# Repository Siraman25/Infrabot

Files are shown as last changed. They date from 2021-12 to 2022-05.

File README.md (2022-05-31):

# **Infrarot-Roboter**
## **Beschreibung**
Bei diesen Inrarot-Robotern handelt es sich um zwei auf Rädern fahrenden Robotern welche als "Shooter-Spiel" konzipiert sind. Sie werden über zwei ESP-32 gesteuert (ESP32-CAM & ESP32-S2). Bedient werden sie entweder mit einem PS3-Controller oder über eine Website via PC oder Smartphone. Die Steuerung über PS3-Controller wird durch eine Bluetooth-Verbindung zwischen Controller und ESP32-S2 realisiert.\
Sie können sich gegenseitig abschießen. Dies wird mit Infrarot-Empfänger und -Sender realisiert. Für ein akustisches Feedback für Fehler, Schuss und Treffer werden Buzzer verwendet.\
Die Räder werden mit zwei 360°-Servomotoren angetriebn. Diese besitzen drei Pins: GND, +5V, Steuersingal. Die beiden Pins GND und +5V werden direkt an den Spannungsregler angeschlossen, da ein Servomotor ca. 550mA Strom zieht. Der Pin für das Steuersignal wird an den ESP32-S2 angeschlossen.\
Über eine Webseite, die auf dem ESP-S2 läuft, kann man den Videostream des ESP-CAM sehen.

Der Ordner "ESP32-CAM Code" enthält das funktionierende Code, im "Debug Code" Ordner befinden sich unwichtige Programme und Sketches, die wir fürs Debugging und fürs Testen benutzt haben. Der Ordner "ESP32-S2 Code" enthält das getestete Code für den ESP32-S2, dieser sollte einwandfrei funktionieren. Leider konnten wir es nicht aufbauen. Im "Web-Interface"-Ordner befindet sich der Boilerplate für die Web-Interface und eine kleine Dokumentation, wie das ausschauen hätte sollen. Dazu gibt es noch den Doku-Ordner.

## **Beschreibung**
##### Servo
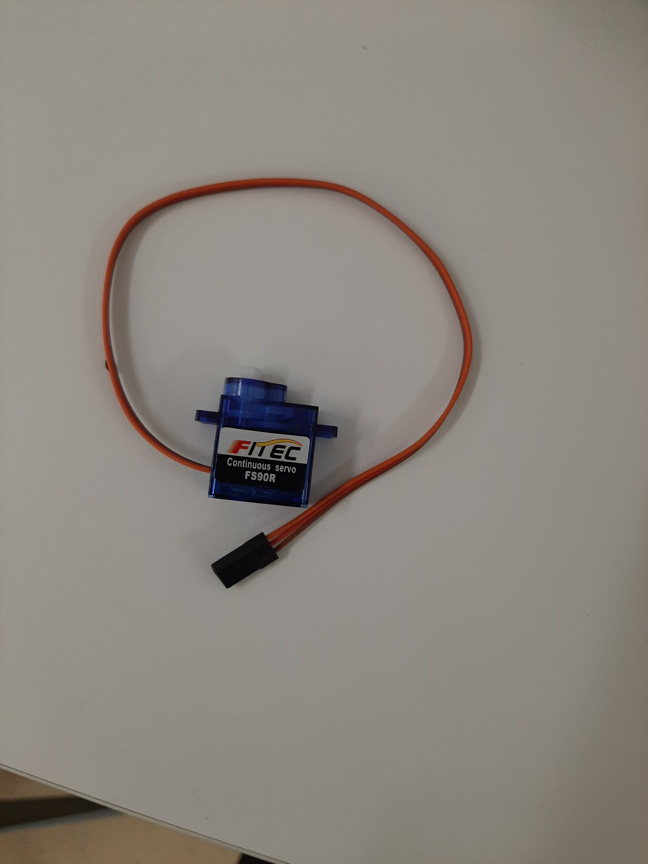
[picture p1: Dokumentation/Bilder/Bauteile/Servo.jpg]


<code>Name</code>: Continous servo FS90R
<code>Preis</code>: € 21,81	(4 Stück)
<code>Link</code>: [Click-here](https://it.aliexpress.com/item/32984667875.html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)
##### Batteriehalterung
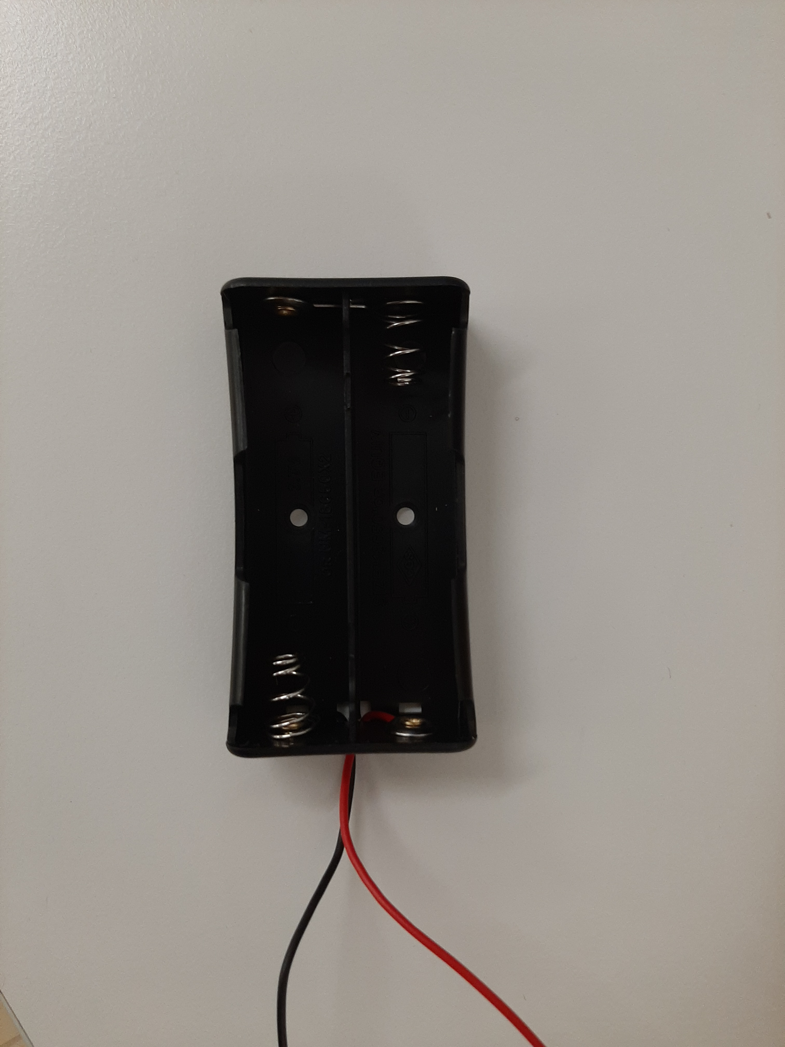
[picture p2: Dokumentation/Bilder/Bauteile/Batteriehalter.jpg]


<code>Name</code>: 
<code>Preis</code>: 
<code>Link</code>: [Click-here]()
##### Powermanagement

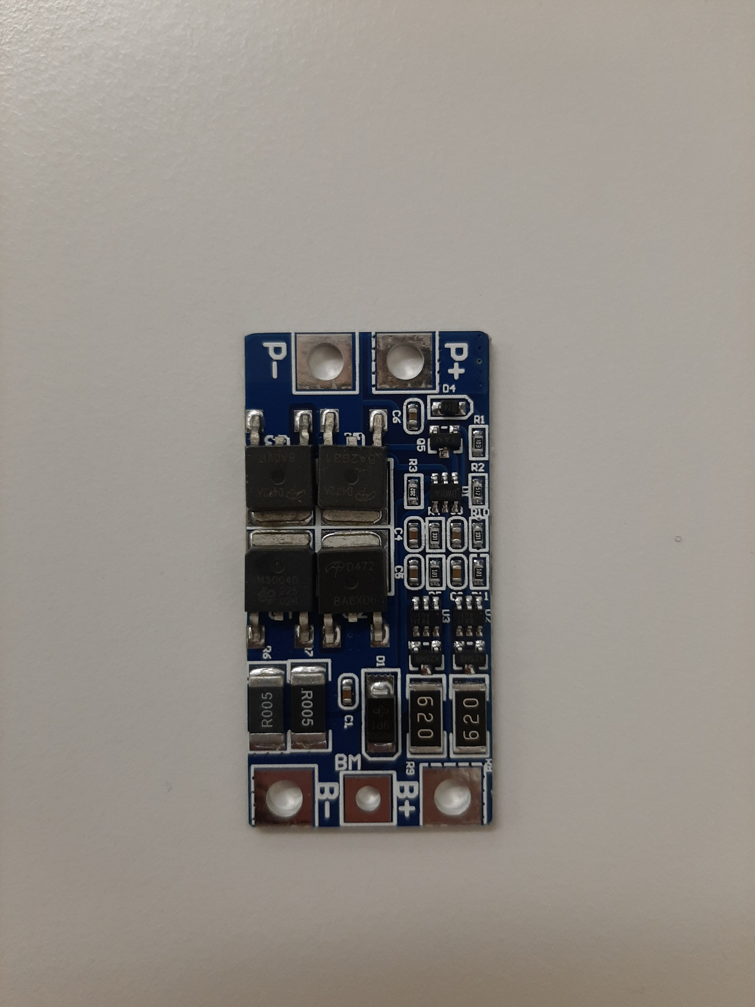
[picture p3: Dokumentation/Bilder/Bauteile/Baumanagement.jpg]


<code>Name</code>: 
<code>Preis</code>: 
<code>Link</code>: [Click-here]()
##### ESP32 Cam-Module
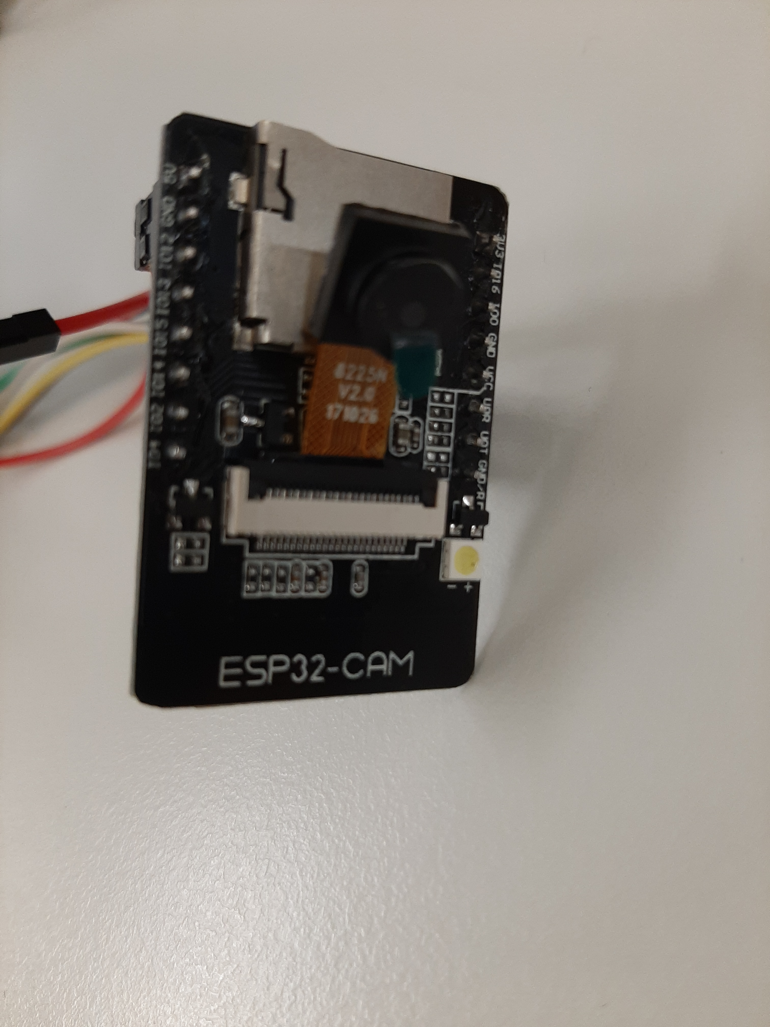
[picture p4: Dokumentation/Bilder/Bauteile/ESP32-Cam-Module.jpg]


<code>Name</code>: 113990580
<code>Preis</code>: € 8,99000 (1 Stück)
<code>Link</code>: [Click-here](https://www.digikey.it/it/products/detail/seeed-technology-co-ltd/113990580/9697033)
##### Hilfsrad
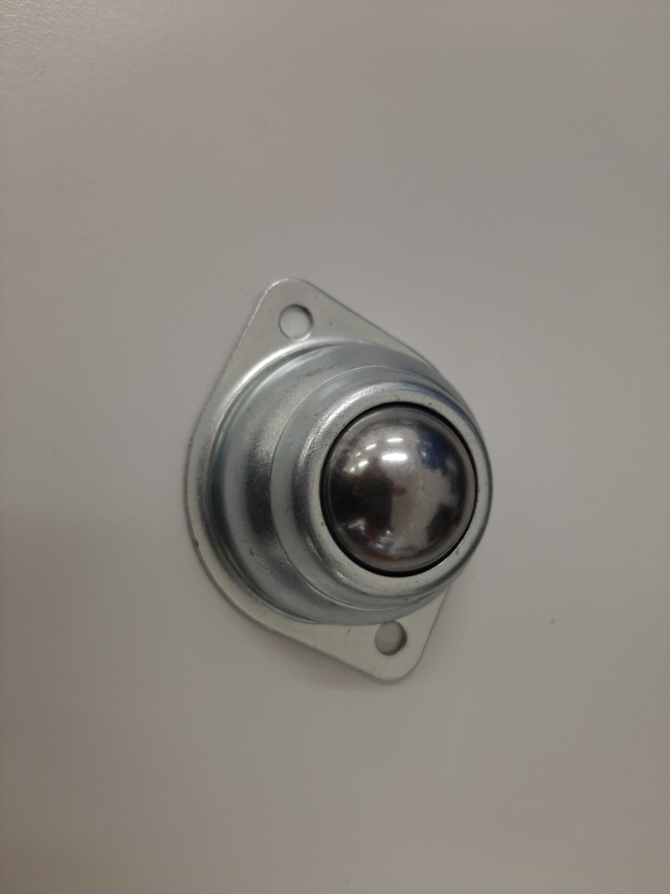
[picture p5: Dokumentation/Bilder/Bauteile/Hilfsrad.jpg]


<code>Name</code>:  Universalrad
<code>Preis</code>:  € 5,95
<code>Link</code>: [Click-here](https://it.aliexpress.com/item/4001072165757.html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,scm-url:1007.13338.183347.0,pvid:666dd3e0-f355-4ce7-bd33-32656806e43c,tpp_buckets:668%232846%238111%231996&&pdp_ext_f=%7B%22sceneId%22:%2223416%22,%22sku_id%22:%2210000014060064385%22%7D)
##### Infrarot LED
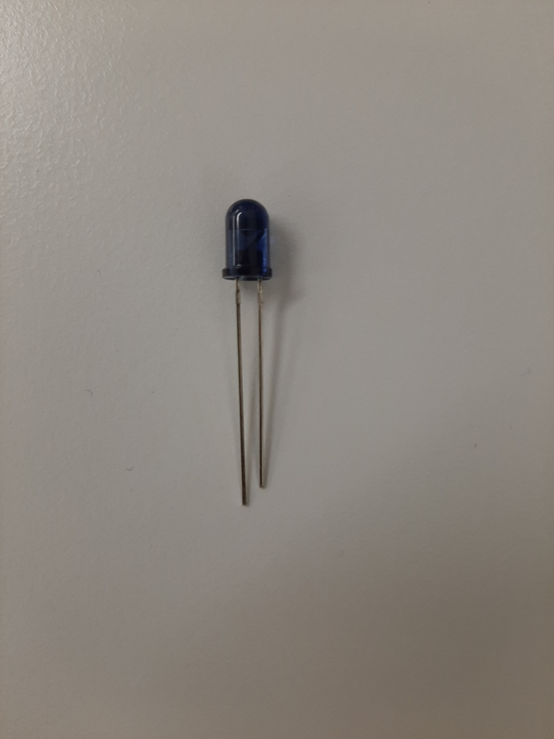
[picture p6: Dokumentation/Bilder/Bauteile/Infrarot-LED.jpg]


<code>Name</code>: # TSAL6100
<code>Preis</code>: € 0,47000 (1 Stück)
<code>Link</code>: [Click-here](https://www.digikey.it/it/products/detail/vishay-semiconductor-opto-division/TSAL6100/1681338)
##### Infrarot Reciever
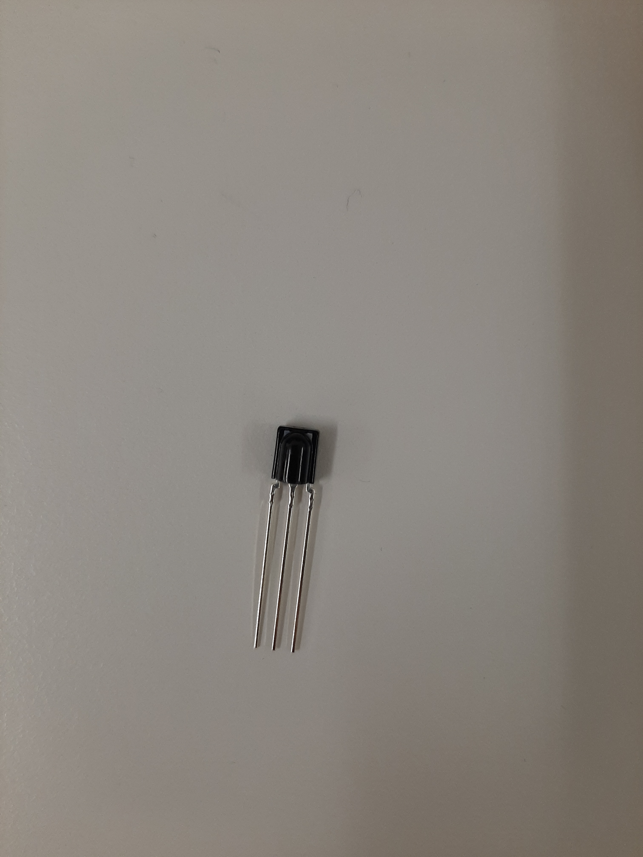
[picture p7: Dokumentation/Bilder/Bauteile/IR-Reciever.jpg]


<code>Name</code>: TSSP58038
<code>Preis</code>: € 1,42000 (1 Stück)
<code>Link</code>: [Click-here](https://www.digikey.it/it/products/detail/vishay-semiconductor-opto-division/TSSP58038/4695717)
##### Button
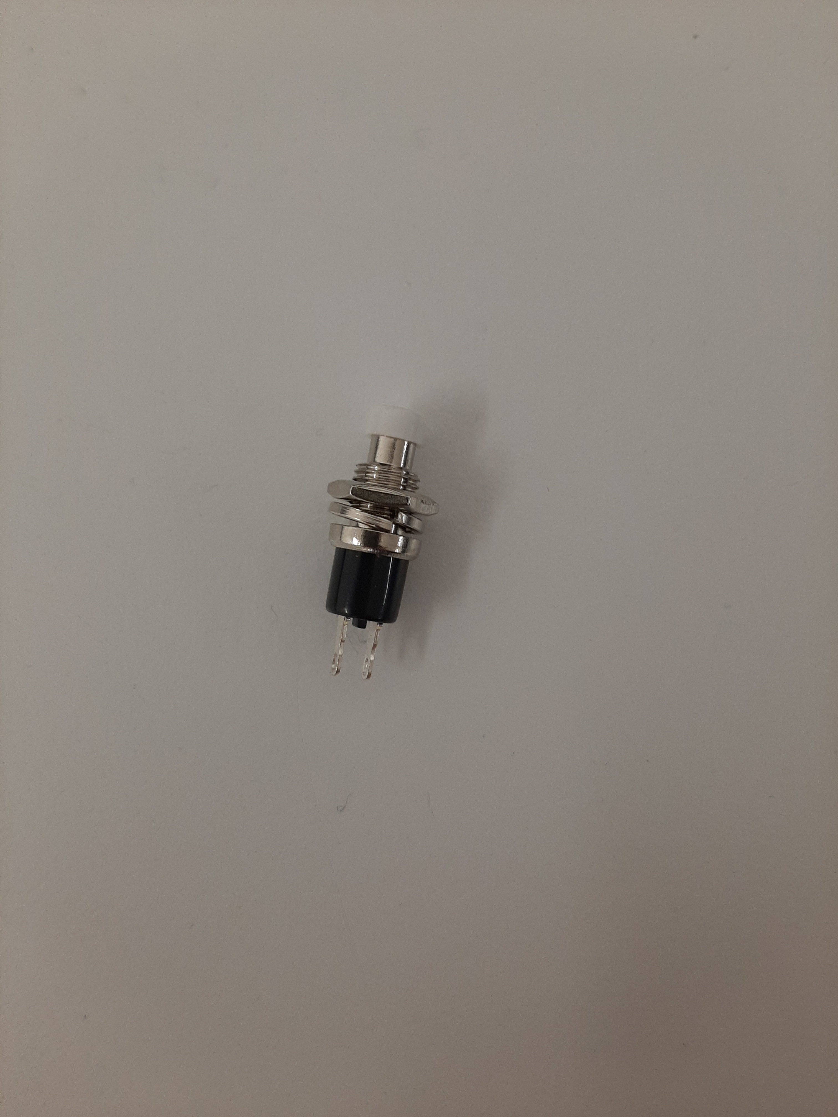
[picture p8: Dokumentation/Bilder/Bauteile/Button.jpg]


<code>Name</code>: 
<code>Preis</code>: 
<code>Link</code>: [Click-here]()
##### Switch
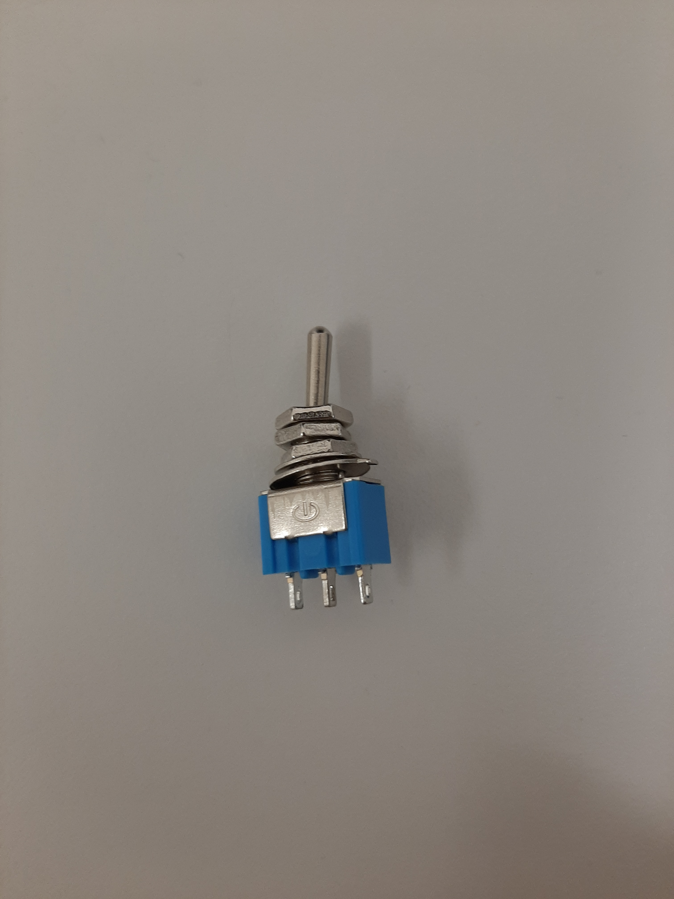
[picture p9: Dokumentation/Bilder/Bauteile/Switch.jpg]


<code>Name</code>: 
<code>Preis</code>: 
<code>Link</code>: [Click-here]()
##### Kühler
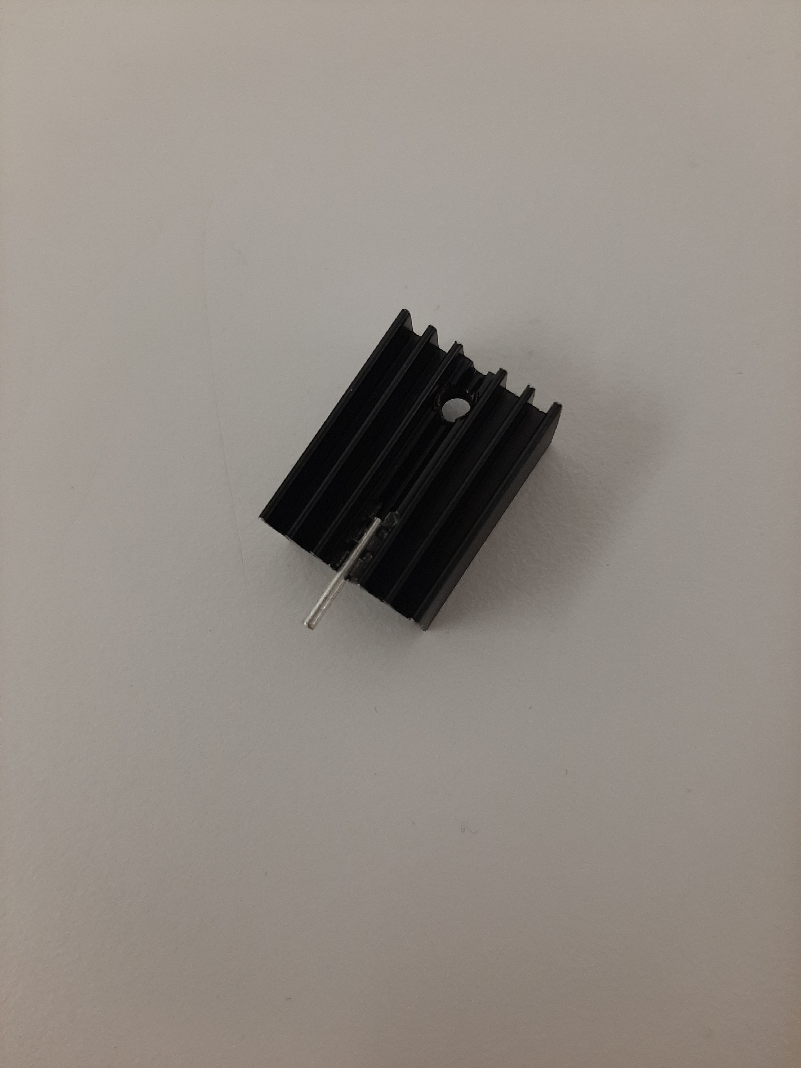
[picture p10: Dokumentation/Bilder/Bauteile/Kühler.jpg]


<code>Name</code>:  PS3-Controller
<code>Preis</code>: 
<code>Link</code>: [Click-here]()
##### Spannungsregler
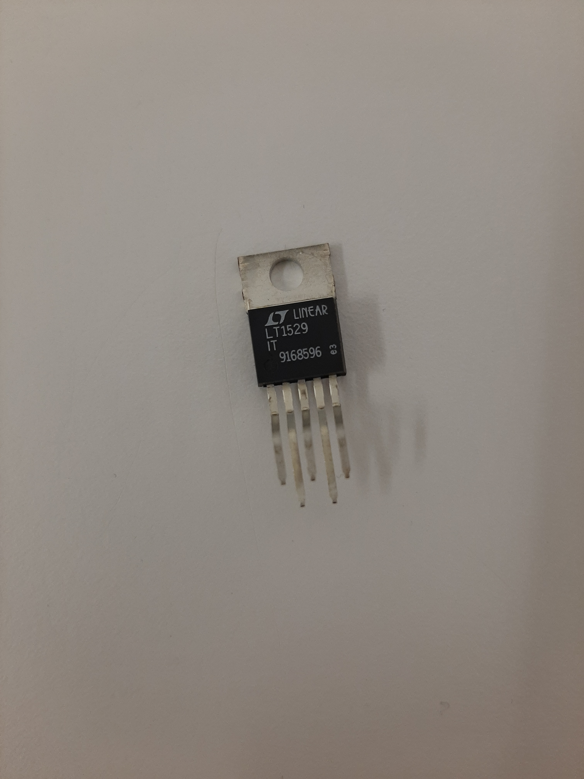
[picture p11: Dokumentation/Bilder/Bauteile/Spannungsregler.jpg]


<code>Name</code>:  LT1529-5
<code>Preis</code>: 
<code>Link</code>: [Click-here]()

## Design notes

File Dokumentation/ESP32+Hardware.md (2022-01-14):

#PS3-Controller
##Funktionen
Der Linke Joystick ist für die steuerung des Robos zuständig

#360° Servo (FS90R)
##Verkabelung
Servo1: Pin D12
Servo2: Pin D14

#Librarys
####Servo.h
#### GitHub: https://github.com/RoboticsBrno/ServoESP32
####PS3_Controller_Host-1.1.0

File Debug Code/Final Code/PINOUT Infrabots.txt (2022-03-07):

PINOUT Infrabots:

ESP32-S2
GND -> GND_PLATINE
5V -> 5V_PLATINE
3.3V -> 3.3V_PLATINE
38 -> RESET_PIN_IN
39 -> IR_REC
40 -> IR_SEND
41 -> HWSerial_0       (RX S2, TX CAM)
42 -> HWSerial_1       (TX S2, RX CAM)

ESP32-CAM
GND -> GND_PLATINE
U0T -> SERIAL_TX_UPLOAD
U0R -> SERIAL_RX_UPLOAD
IO0 -> PIN0_UPLOAD
3.3V -> 3.3V_PLATINE
IO2 -> SERVO1
IO14 -> HWSerial_0      (TX S2, RX CAM)
IO13 -> HWSerial_1      (RX S2, TX CAM)
IO12 -> SERVO2
5V -> 5V_PLATINE

Alle GNDs der einzelnen Boards müssen sicherheitshalber auf der Platine verbunden werden.

Weitere Verbindungen:
IR_SEND:
IR_SEND -> BC337 (Transistor) Base // 3.3V_PLATINE -> BC337 Collector // BC337 Emitter -> IR-LED -> 20 OHM-Widerstand (2*10 Ohm) -> GND_PLATINE

IR_REC:
IR-Receiver+ -> 5V_PLATINE // IR-Receiver- -> GND_PLATINE // IR-Receiver_DATA -> IR_REC

SERVOS:
SERVO+ -> 5V_PLATINE // SERVO- -> GND_PLATINE // SERVO_DATA -> SERVOxx

RESET_PIN_IN:
GND_PLATINE -> 10kOhm -> RESET_PIN_IN (Pull-down-Widerstand) // Switch-button+ -> 5V_PLATINE // Switch-button- -> RESET_PIN_IN

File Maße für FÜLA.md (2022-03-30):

- Platine:
	- Länge= 127mm
	- Breite= 65mm
	- Höhe= 2mm
- Hinterrad:
	- Durchmesser<sub>GROẞ</sub>= 70mm
	-  Durchmesser<sub>KLEIN</sub>= 52mm
	-  Höhe= 30mm
	-  Durchmesser Kugel= 40mm
-  Servo:
	-  Länge= 23mm
	-  Breite= 22mm
	-  Höhe= 12mm
		-  Ecken:
			-  Länge= 3mm
			-  Breite= 5mm
			-  Höhe= 12mm
			-  Versatz Vorderkante= 4mm
-  Vorderrad:
	-  Durchmesser= 60mm
	-  Breite= 7mm
-  Batteriebehälter
	-  Länge= 75mm
	-  Breit= 40mm
	-  Höhe= 18mm

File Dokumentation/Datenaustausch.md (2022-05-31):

# Datenaustausch
Der PS3-Controller wird über Bluetooth mit ESP32-CAM verbunden. Der ESP32-CAM steuert die beiden Servos. Der ESP-S2 ist über Hardware-Serial mit dem ESP32-CAM verbunden. Für das Empfangen und Senden des Infrarotsignals ist der ESP32-S2 zuständig.\
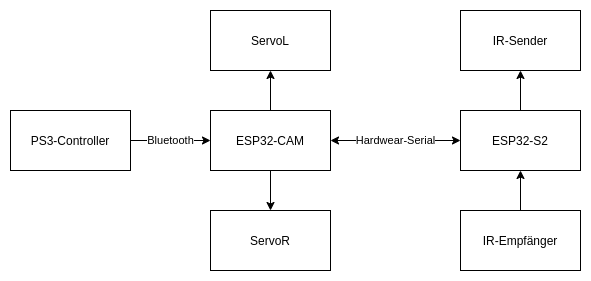
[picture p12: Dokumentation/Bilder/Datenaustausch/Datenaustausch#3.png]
Datenaustausch
 

Da wir den ESP32-S2 nicht implementiert haben funktioniert der Infrarot nicht und die ganze rechte Seite dieses Bildes wird nicht benötigt.

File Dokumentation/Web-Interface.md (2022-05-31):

# Web-Interface
Die Web-Interface zeigt das Video-Feed des ESP32-CAM-Moduls, im Code vom ESP32-CAM werden die verschiedenen Video-Einstellungen eingestellt.
Die originelle Idee wäre die gewesen, dass man den Punktestand der zwei Roboter sieht. Diese Funktion wurde allerdings nicht implementiert, da es ohne Infrarot-System (bzw. ohne 2. Roboter) keinen Sinn ergibt, die Punkte zu zählen.
Als basis der HTML-Datei wurde die standard-Library des ESP32-CAM benutzt. Dann wurde der Container des Video-Feeds geändert, um die Möglichkeit, vom Browser Einstellungen zu ändern, zu entfernen.

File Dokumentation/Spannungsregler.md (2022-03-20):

# Spannungsregler

Verwendeter Spannungsregler: LT1529

## Charakterisitics
* V<sub>Out</sub>= 3,3V - 14V
* I<sub>Max</sub>= 3A
* V<sub>DropOut<sub>Min</sub></sub> at I<sub>Max</sub>= >0,6V
* Thermisches Limit= 125°

## Verwendung und Package
Package: CT

 Spannungsregler_Package
 
 Verwendung:
 
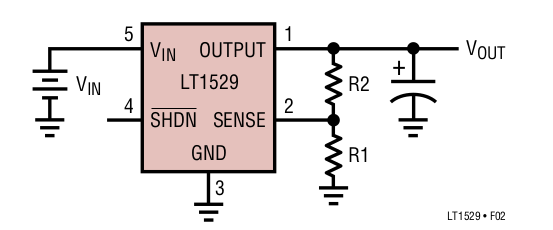
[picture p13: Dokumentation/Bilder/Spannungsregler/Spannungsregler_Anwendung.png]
Spannungsregler_Anwendung
 
 
 ## Pins
 * **OUTPUT**: 
 Dieser Pin Liefert die Spannung (V<sub>Out</sub>) und den Strom für die Last. Der 22$\mu$F Elektrolykondensator wird verwendet um Schwingungen zu vermeiden.
 * **SENSE**:
 Dieser Pin ist auch als ADJ-Pin bekannt. Zur Wahl der Ausgangsspannung wird hier ein Spannungsteiler eingebaut.
 * **GND**:
 Über den GND-Pin fällt die Spannung V<sub>DO</sub> ab. V<sub>DO</sub> ist die Differenz zwischen V<sub>In</sub> und V<sub>Out.
 * **<span style="text-decoration:overline">SHDN</span>**: 
 Der <span style="text-decoration:overline">SHDN</span> Pin ist für das Ein- bzw. Ausschalten des Gerätes zuständig. Bekommt diser Pin ein High-Signal so ist der Spannungsregler aktiv. Bei einem Low-Signal ist er inaktiv.
 * **V<sub>IN</sub>**:
 V<sub>IN</sub> ist der Input-Pin. Über ihn fließt die zu regulierende Eingangspannung (V<sub>In</sub>).

## Berechnung des Spannungsteilers
**Gegeben:**
U<sub>OUT</sub>= 5V\
U<sub>R1</sub>= 3,75V\
U<sub>R2</sub>= 1,25V\
I<sub>SENSE</sub>= 150nA
	
**Wahl:**
R<sub>1</sub>= 100kΩ
	
**Rechnung:**
	I<sub>R1</sub> = U<sub>R1</sub> : R<sub>1</sub> -> 3,75V : 100kΩ = 37,5µA\
	I<sub>R2</sub> = I<sub>R1</sub> - I<sub>SENSE</sub> -> 37,5µA - 150nA = 37,35µA\
	R<sub>2</sub> = U<sub>R2</sub> : I<sub>R2</sub> -> 1,25V : 37,35µA = 33467,202Ω ≈ 33kΩ
	
**Probe:**
	U<sub>OUT</sub> = U<sub>R1</sub> x (1 + (R<sub>2</sub> : R<sub>1</sub>)) + (I<sub>SENSE</sub> x R<sub>2</sub>) -> 3,75V x (1 + (33kΩ : 100kΩ)) +(150nA x 33kΩ) = 4,99245V
	
## Thermische Probleme

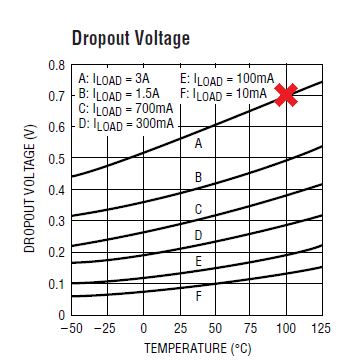
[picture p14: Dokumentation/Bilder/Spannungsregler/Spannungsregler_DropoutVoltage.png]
Spannungsregler_DropoutVoltage

	
Bei einem maximalen Ausgangsstrom von 3A und einer Abfallsspannung von 0,7V erreicht der Spannungsregler eine Temperatur von 100°. Da wir unseren aber mit einer höheren Abfallsspannung zurechtkommen muss, werden wir ohne Kühlung das thermische Limit von 125° überschreiten. Um eine thermische Zerstörung zu vermeiden verwende wir einen Kühler für das Package TO-220. 

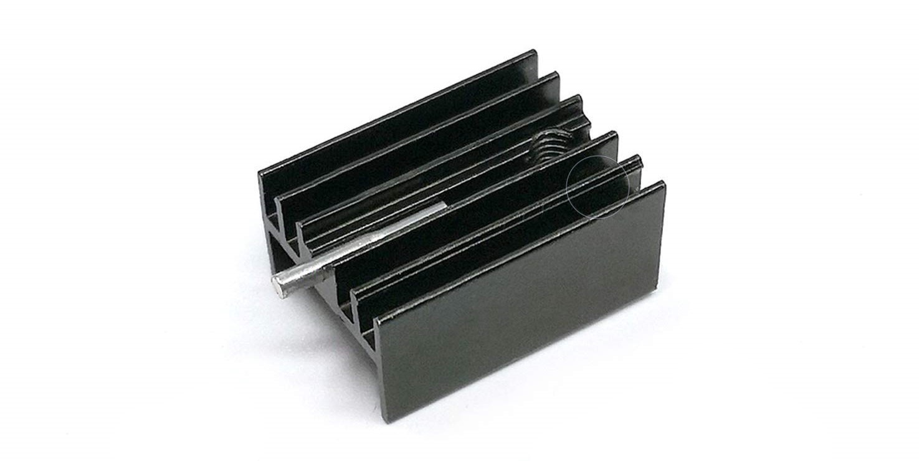
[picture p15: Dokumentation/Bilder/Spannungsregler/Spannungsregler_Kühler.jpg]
Spannungsregler_Kühler


Dies ist ein Low-Profile Aluminium Kühlkörper, der P<sub>Kühler</sub> = 3W Leistung and die Umgebung abgibt.
	
## **Leistungsberechnung**
	
Thermischer Widerstand:
Spannungsregler_ThermischerWiderstand
	
**Gegeben:**
	V<sub>In</sub> = 6,7V\
	V<sub>OUT</sub> = 5V
	I<sub>GES</sub> = 2,5A\
	P<sub>Kühler</sub> = 3W\
	T<sub>Umgebung</sub>≈ 30°C\
	
**Rechnung:**
	U<sub>DropOut</sub> = V<sub>In</sub> - V<sub>Out</sub> -> 6,7V - 5V = 1,7V\
	P<sub>GES</sub> = U<sub>DropOut</sub> x I<sub>GES</sub> -> 1,7V x 2,5A = 4,25W\
	P<sub>VR</sub> = P<sub>GES</sub> - P<sub>Kühler</sub> -> 4,25W - 3W = 1,25W\
	T<sub>VR</sub> = P<sub>VR</sub> x 50°C/W -> 1,25W x 50°C/W = 62,5°C\
	T<sub>GES</sub> = T<sub>Umgebung</sub> + T<sub>VR</sub> -> 30°C + 62,5°C = 92,5°C

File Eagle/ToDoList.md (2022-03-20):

- [ ]   extra Pins
- [ ]   extra Leds (statusleds)
- [ ]   virtual serial
- [ ]   Vorwiedertsände berechnen
- [ ]   pins für buzzers
- [ ]   Löcher an den Ecken zur Fixierung der Platine

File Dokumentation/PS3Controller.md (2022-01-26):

# Steuerung der Motoren mit einem Ps3 Controller

## **Biblioteken**

> **Ps3_Controller.h** (https://github.com/jvpernis/esp32-ps3)

* <code>Ps3.begin("MAC_Adresse");</code> ist dazu da die mac adresse des Ps3controllers dem esp32 zu geben, damit dieser sich mit dem Controller verbinden kann.
* <code>Ps3.attachOnConnect(onConnect);</code> ist dazu da in einem void **(onConnect)** zu springen aus dem erst wieder herrausgesprungen wird sobalt der Controller verbunden ist.
* <code>Ps3.attach(notify);</code> ist dazu da in den void **(notify)** zu springen wo die Knöfe und Joysticks des Controllers ausgelesen werden.
* <code>Ps3.event.analog_change.button.l1</code> ist dazu da den shoulderbutton in einem analogwert auszulesen. das **l1** am ende kann mit **r1**, **r2**, **l2** ausgewechselt werden je nachdem welcher button ausgelesen werden soll.
* <code>Ps3.data.analog.stick.rx</code>: dieser Befehl ließt die Werte des Joysticks aus. **rx** kann mit **ry**, **ly**, **lx** ausgewechselt werden je nachdem welcher Joystick und welche achsen des Joysticks benötigt werden. Die X-Achse gibt werte von **-128(links)** bis **127(rechts)** aus.Die Y-Achse gibt auchh die Werte **-128(vorne)** bis **127(hinten)** aus.
* <code>Ps3.data.button.cross</code>: dieser Befehl liest den **X** button auf der rechten Seite des Controllers aus. Wenn mann **"cross"** mit **"triangle"**, **"square"** oder **"circle"** austauscht werden die andern 3 buttons ausgelesen.

>  **Servo.h** (https://www.arduino.cc/reference/en/libraries/servo/) 
* <code>servo[].write("0,90 oder 180");</code> Diese Funktion ist dafür da den Servo die Informationen zu geben in welche richtung er sich drehen soll. In den Klammern wird **90** geschrieben fals der Servo stehen bleiben soll, **180** wenn er sich mit höchster geschwindigkeit in eine Richtung bewegen soll und **0** wenn er mit höchster geschwindigkeit in die andere Richtung fahren soll. 
* <code>static const int servosPins[2]; = {"PinSero1, PinServo2"};</code> In dieser Funktion werden die Pins an denen die Servos angeschlossen werden declariert. 
* <code>Servo servos[2];</code> In den eckigen Klammern wir die anzahl wie viele Servos verwendet werden angegeben.

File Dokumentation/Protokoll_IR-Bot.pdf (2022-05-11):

Aris Mandolini | Juri Ladurner | Max Dandler

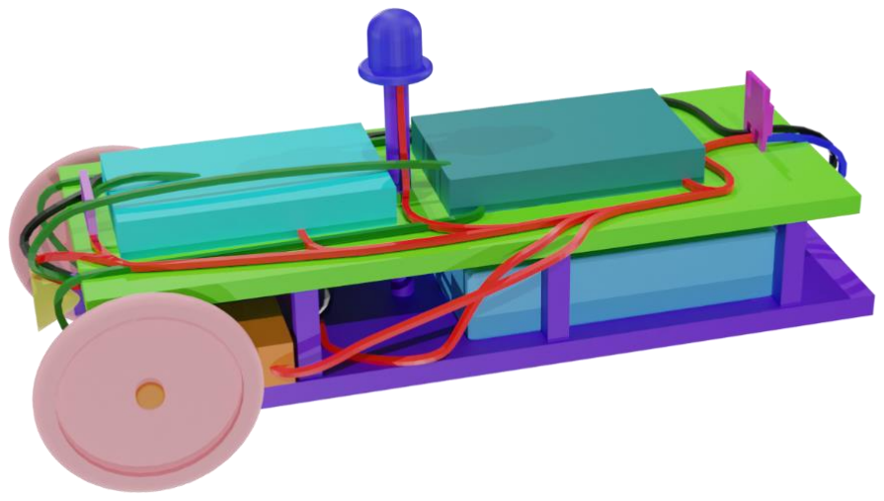
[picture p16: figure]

FÜLA: IR-Bot | 2021/22

## IR-Bot

Protokoll

Anlagenschema:

Beschreibung:

Dieses Projekt besteht aus zwei identischen Fahrzeugen. Es sind zwei fahrbare Roboter, welche auf drei Rädern stehen. Die beiden vorderen Rädern sind an 360°-Servos gekoppelt, welche für die Bewegung des Roboters verantwortlich sind. Das hintere Rad ist nur zur Stabilisierung da. Gesteuert wird der Roboter mithilfe eines PS3-Controllers. Dieser verbindet sich via Bluetooth an den ESP32-Cam. Der ESP32-Cam steuert auch die beiden Servo-Motoren. Der ESP32-Cam ist mit Hardware-Serial mit dem ESP32-S2 verbunden und erhält über diese Datenlinie Daten vom ESP32-S2. Der ESP32-S2 steuert den Infrarot-Receiver und den Infrarot-Transmitter. Der Infrarot-Transmitter ist das “Gewehr” des Roboters. Der Receiver empfängt die ausgesandten Lichtwellen.

HMI:

schießen

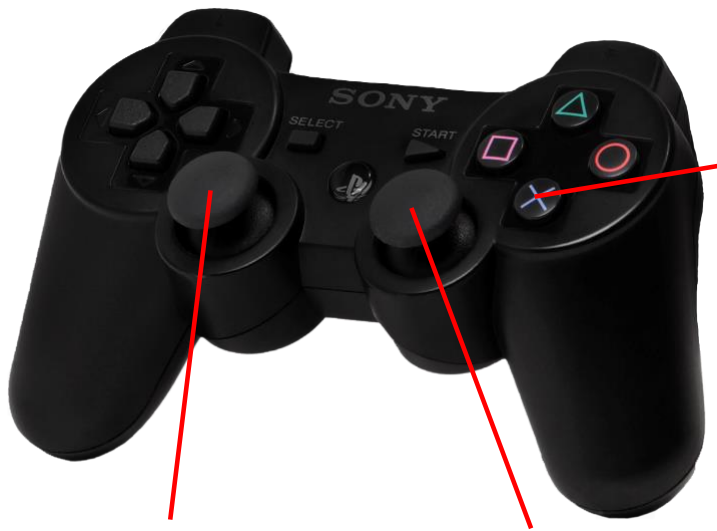
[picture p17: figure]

Servo-Links | Servo-Rechts

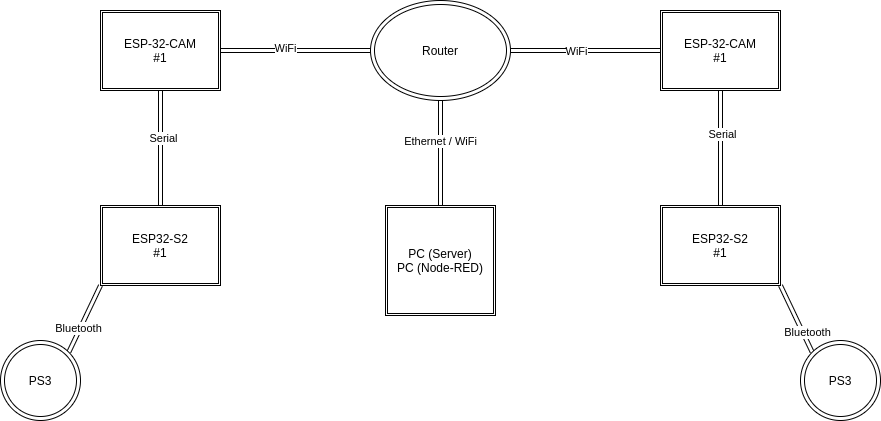
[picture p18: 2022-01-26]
Web-Interface/Network.drawio.png

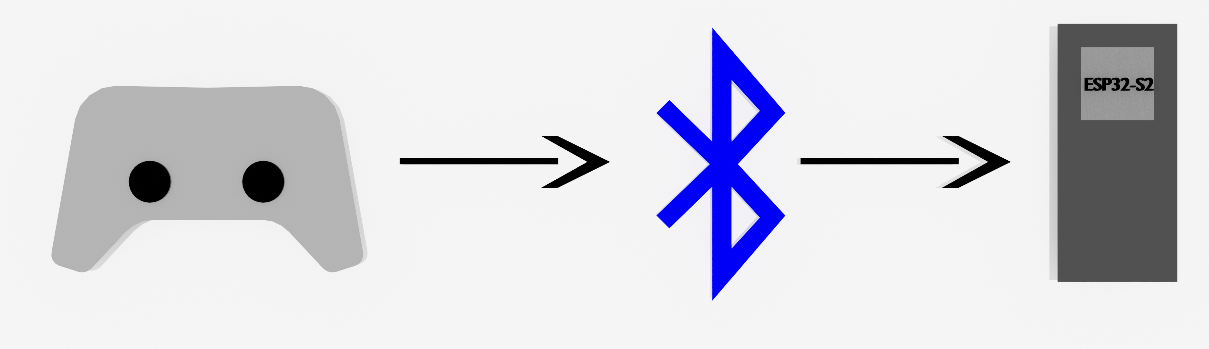
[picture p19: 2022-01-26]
Dokumentation/Bilder/Readme/Connection_PS3_ESP32.png

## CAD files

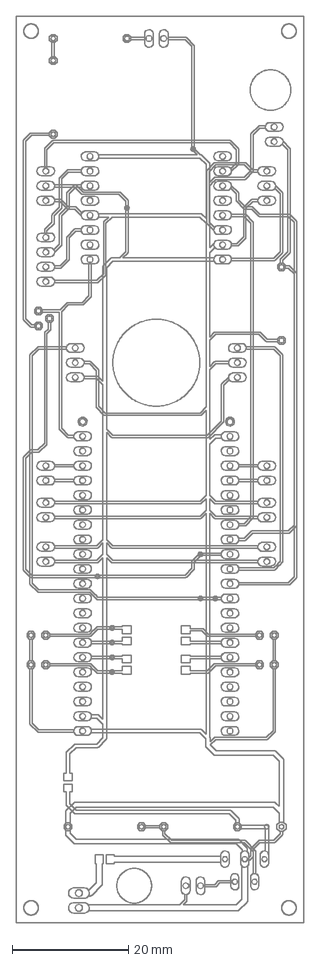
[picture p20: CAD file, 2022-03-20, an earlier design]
Eagle/V3/Spannungsversorgung_V3_#3.dxf
49.5 x 156.2 mm

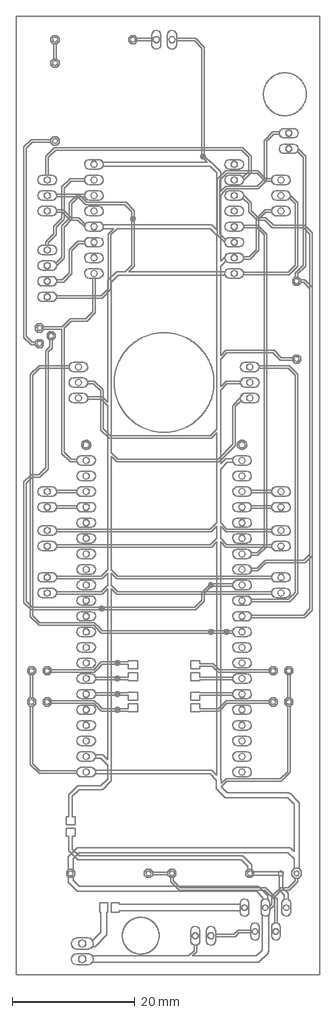
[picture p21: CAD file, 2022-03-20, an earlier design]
Eagle/V3/Spannungsversorgung_V3_#2.dxf
49.5 x 156.2 mm

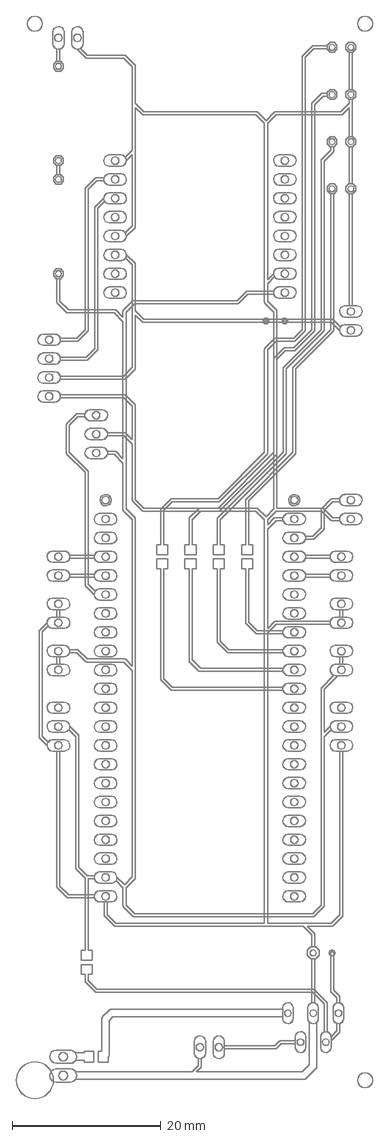
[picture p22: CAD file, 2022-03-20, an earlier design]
Eagle/V3/Spannungsversorgung_V3_#1.dxf
48.0 x 145.7 mm

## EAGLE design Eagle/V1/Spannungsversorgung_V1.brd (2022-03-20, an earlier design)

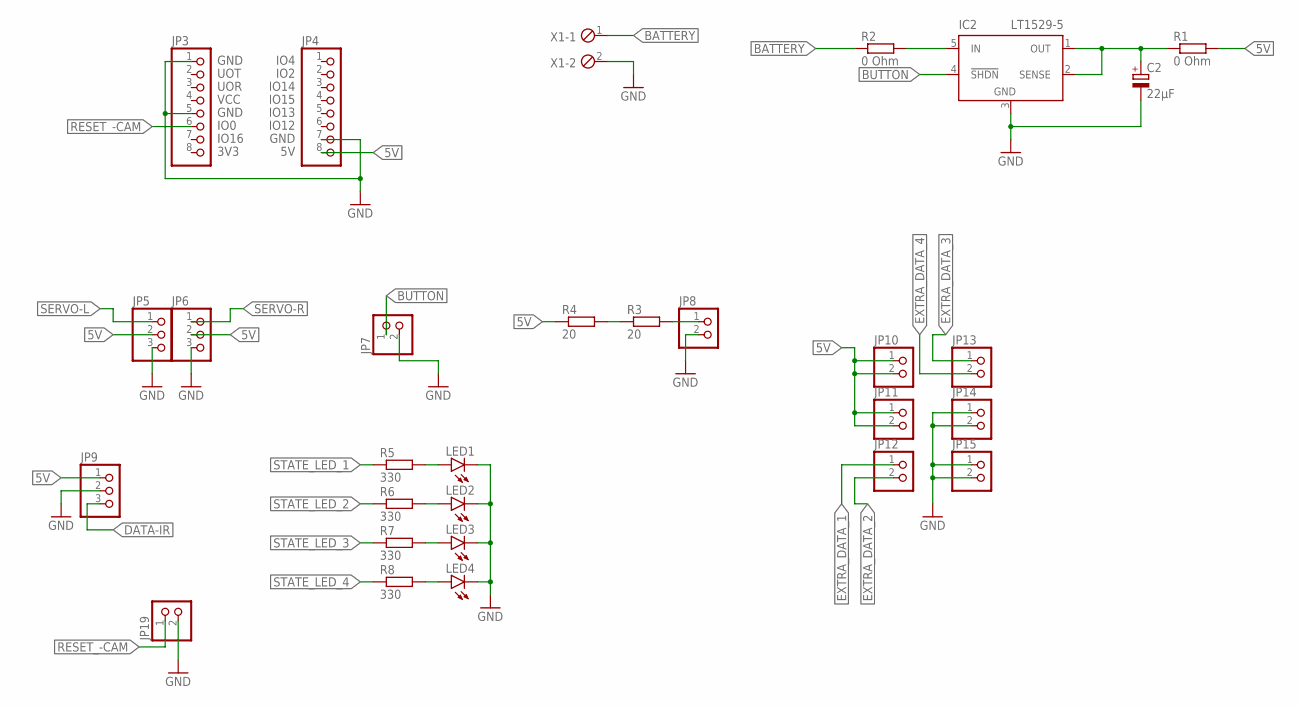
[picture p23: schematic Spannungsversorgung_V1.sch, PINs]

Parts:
C2: 22µF; E2,5-5
IC2: LT1529-5; TO220-5
JP3, JP4: PINHD-1X8; 1X08
JP5, JP6, JP9: PINHD-1X3; 1X03
JP7, JP8, JP10, JP11, JP12, JP13, JP14, JP15, JP19: PINHD-1X2; 1X02
LED1, LED2, LED3, LED4: LED3MM
R1, R2: 0 Ohm; R0805
R3, R4: 20; 0309/12
R5, R6, R7, R8: 330; R0805
X1: MPT2; 2POL254

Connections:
5V: JP4.8, JP5.2, JP6.2, JP9.1, JP10.1, JP10.2, JP11.1, JP11.2, R1.2, R4.1
BATTERY: R2.1, X1.1
BUTTON: IC2.4 (!SHDN), JP7.1
DATA-IR: JP9.3
EXTRA_DATA_1: JP12.1
EXTRA_DATA_2: JP12.2
EXTRA_DATA_3: JP13.1
EXTRA_DATA_4: JP13.2
GND: C2.-, IC2.3 (GND), JP3.1, JP3.5, JP4.7, JP5.3, JP6.3, JP7.2, JP8.2, JP9.2, JP14.1, JP14.2, JP15.1, JP15.2, JP19.2, LED1.K (C), LED2.K (C), LED3.K (C), LED4.K (C), X1.2
unnamed: R3.1, R4.2
unnamed: JP8.1, R3.2
unnamed: IC2.5 (IN), R2.2
unnamed: C2.+, IC2.1 (OUT), IC2.2 (SENSE), R1.1
unnamed: LED1.A, R5.2
unnamed: LED2.A, R6.2
unnamed: LED3.A, R7.2
unnamed: LED4.A, R8.2
RESET_-CAM: JP3.6, JP19.1
SERVO-L: JP5.1
SERVO-R: JP6.1
STATE_LED_1: R5.1
STATE_LED_2: R6.1
STATE_LED_3: R7.1
STATE_LED_4: R8.1

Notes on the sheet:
3V3
IO16
IO0
GND
VCC
UOR
UOT
IO12
IO13
IO15
IO14
IO2
IO4

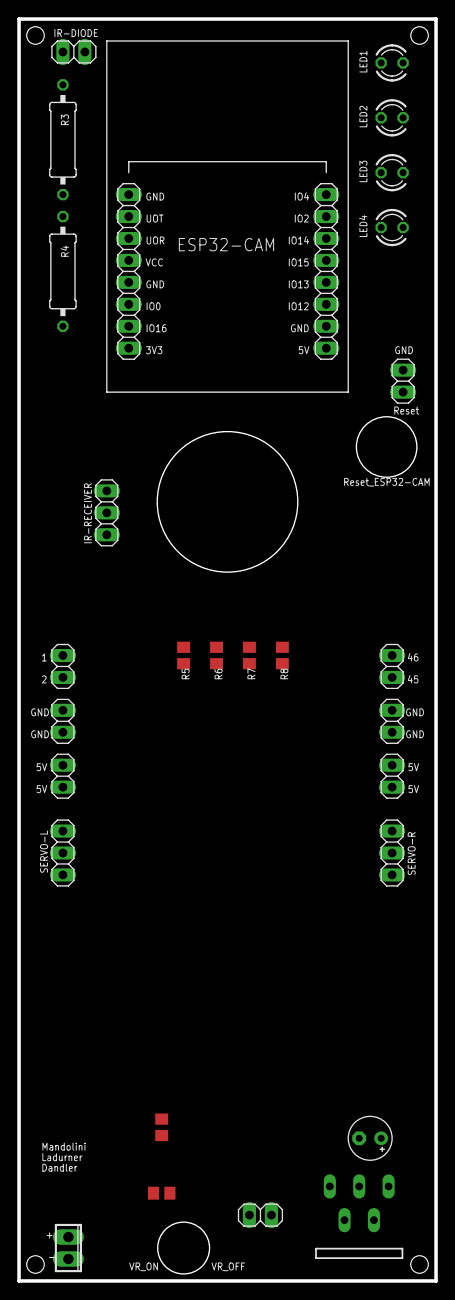
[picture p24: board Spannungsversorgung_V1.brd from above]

Board: 2 copper layers, 48.3 x 146.1 mm, 29 parts (0 on the bottom side), 13 nets.

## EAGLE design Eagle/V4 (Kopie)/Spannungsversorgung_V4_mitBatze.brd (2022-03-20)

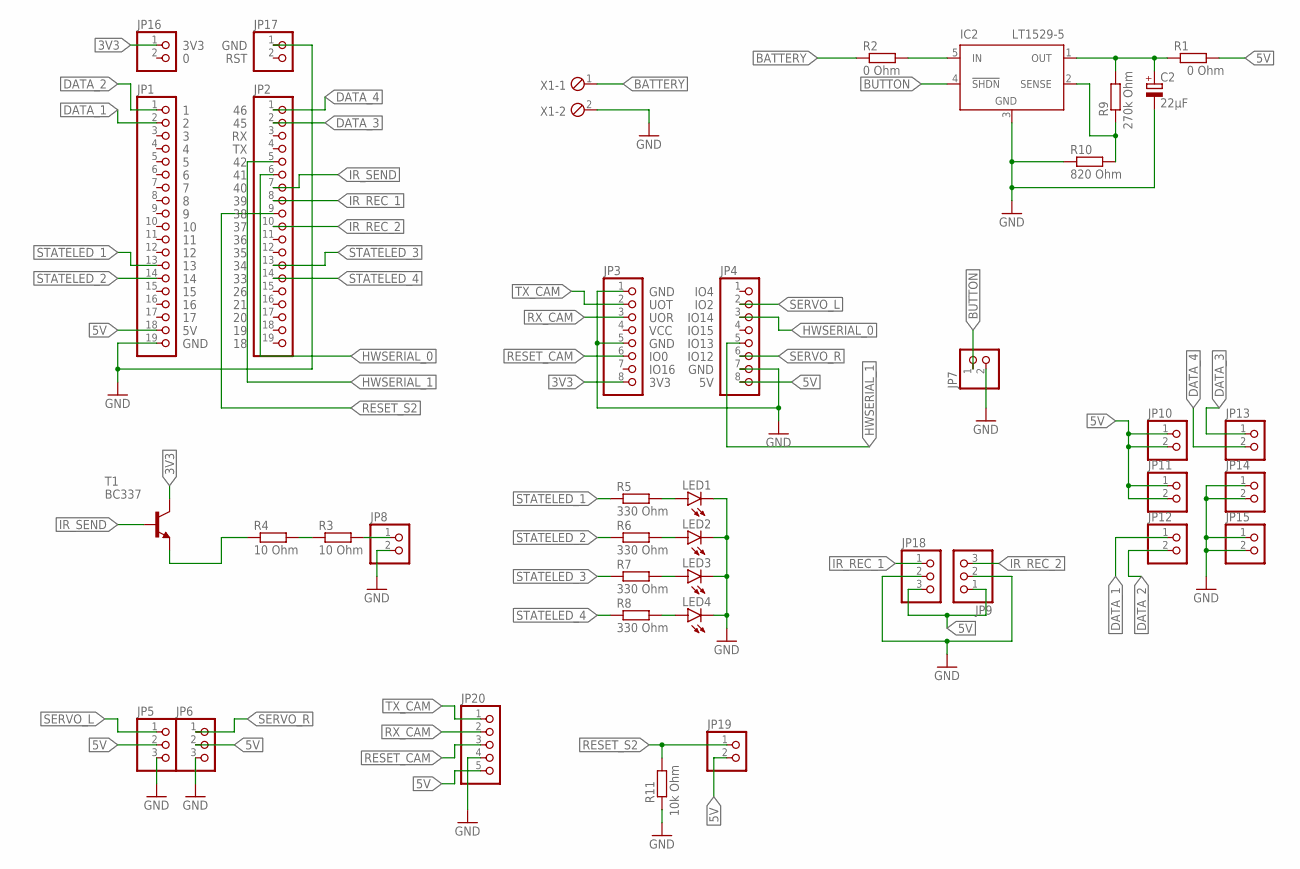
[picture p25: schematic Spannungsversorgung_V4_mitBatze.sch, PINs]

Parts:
C2: 22µF; E2,5-5
IC2: LT1529-5; TO220-5
JP1, JP2: PINHD-1X19; 1X19
JP3, JP4: PINHD-1X8; 1X08
JP5, JP6, JP9, JP18: PINHD-1X3; 1X03
JP7, JP8, JP10, JP11, JP12, JP13, JP14, JP15, JP16, JP17, JP19: PINHD-1X2; 1X02
JP20: PINHD-1X5; 1X05
LED1, LED2, LED3, LED4: LED3MM
R1, R2: 0 Ohm; R0805
R3, R4: 10 Ohm; 0309/12
R5, R6, R7, R8: 330 Ohm; R0805
R9: 270k Ohm; 0309/12
R10: 820 Ohm; 0309/12
R11: 10k Ohm; 0309/12
T1: BC337; TO92
X1: MPT2; 2POL254

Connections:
3V3: JP3.8, JP16.1, T1.3 (C)
5V: JP1.18, JP4.8, JP5.2, JP6.2, JP9.1, JP10.1, JP10.2, JP11.1, JP11.2, JP18.3, JP19.2, JP20.5, R1.2
BATTERY: R2.1, X1.1
BUTTON: IC2.4 (!SHDN), JP7.1
DATA_1: JP1.2, JP12.1
DATA_2: JP1.1, JP12.2
DATA_3: JP2.2, JP13.1
DATA_4: JP2.1, JP13.2
GND: C2.-, IC2.3 (GND), JP1.19, JP3.1, JP3.5, JP4.7, JP5.3, JP6.3, JP7.2, JP8.2, JP9.2, JP14.1, JP14.2, JP15.1, JP15.2, JP17.1, JP18.2, JP20.4, LED1.K (C), LED2.K (C), LED3.K (C), LED4.K (C), R10.1, R11.1, X1.2
HWSERIAL_0: JP2.6, JP4.3
HWSERIAL_1: JP2.5, JP4.5
IR_REC_1: JP2.8, JP18.1
IR_REC_2: JP2.10, JP9.3
IR_SEND: JP2.7, T1.2 (B)
unnamed: R3.1, R4.2
unnamed: JP8.1, R3.2
unnamed: IC2.5 (IN), R2.2
unnamed: LED1.A, R5.2
unnamed: LED2.A, R6.2
unnamed: LED3.A, R7.2
unnamed: LED4.A, R8.2
unnamed: R4.1, T1.1 (E)
unnamed: IC2.2 (SENSE), R9.1, R10.2
unnamed: C2.+, IC2.1 (OUT), R1.1, R9.2
RESET_CAM: JP3.6, JP20.3
RESET_S2: JP2.9, JP19.1, R11.2
RX_CAM: JP3.3, JP20.2
SERVO_L: JP4.2, JP5.1
SERVO_R: JP4.6, JP6.1
STATELED_1: JP1.13, R5.1
STATELED_2: JP1.14, R6.1
STATELED_3: JP2.13, R7.1
STATELED_4: JP2.14, R8.1
TX_CAM: JP3.2, JP20.1

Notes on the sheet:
3V3
IO16
GND
IO0
IO12
IO13
UOR
IO14
VCC
IO15
UOT
IO2
IO4
RST

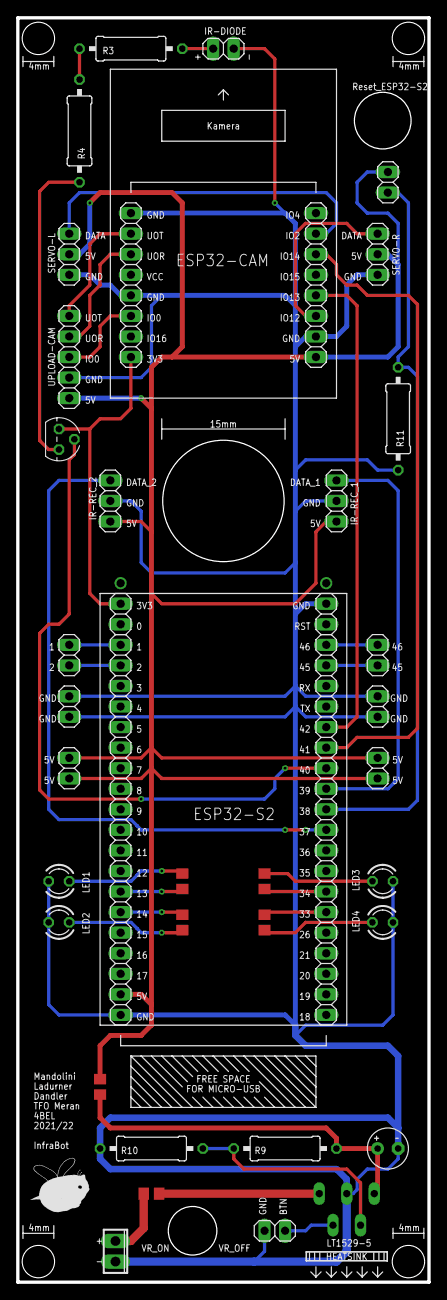
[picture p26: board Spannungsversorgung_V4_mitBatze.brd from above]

Board: 2 copper layers, 50.8 x 156.2 mm, 39 parts (0 on the bottom side), 34 nets.

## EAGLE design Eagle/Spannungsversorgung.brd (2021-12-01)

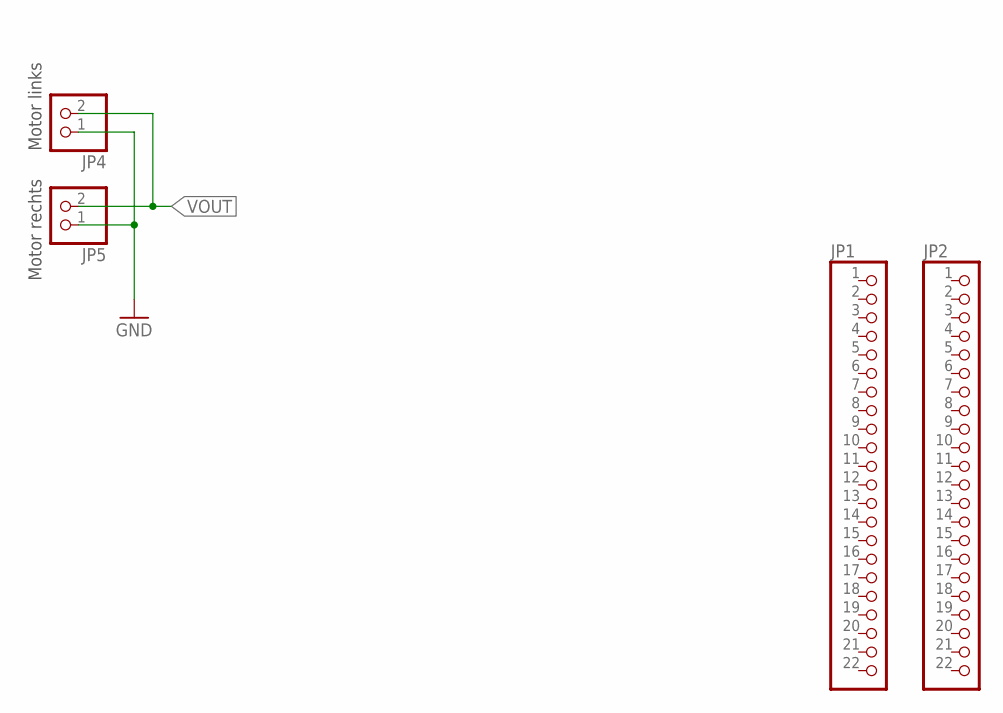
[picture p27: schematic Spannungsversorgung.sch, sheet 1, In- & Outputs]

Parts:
JP1, JP2: PINHD-1X22; 1X22
JP4, JP5: PINHD-1X2; 1X02

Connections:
GND: JP4.1, JP5.1; also elsewhere on the board
VOUT: JP4.2, JP5.2; also elsewhere on the board

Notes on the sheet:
Motor links
Motor rechts

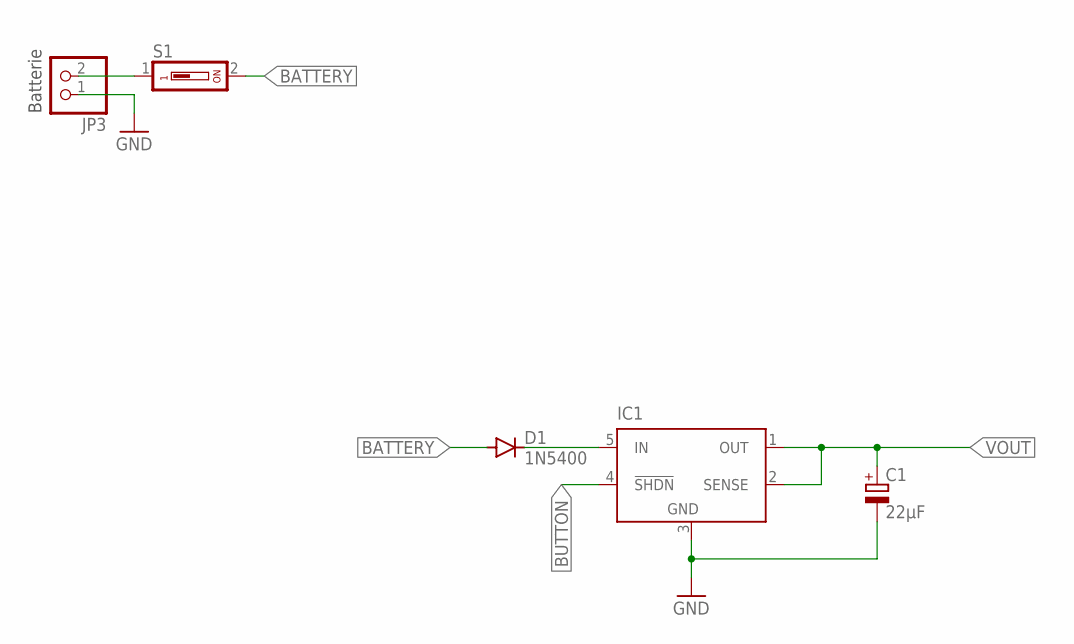
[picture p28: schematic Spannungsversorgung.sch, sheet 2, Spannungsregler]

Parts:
C1: 22µF; E2,5-5
D1: 1N5400; DO201-15
IC1: LT1529T; TO220-5
JP3: PINHD-1X2; 1X02
S1: DS01; DS-01

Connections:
BATTERY: D1.A, JP3.2, S1.1, S1.2
BUTTON: IC1.4 (!SHDN)
GND: C1.-, IC1.3 (GND), JP3.1; also elsewhere on the board
unnamed: D1.C, IC1.5 (IN)
VOUT: C1.+, IC1.1 (OUT), IC1.2 (SENSE); also elsewhere on the board

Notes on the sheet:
Batterie

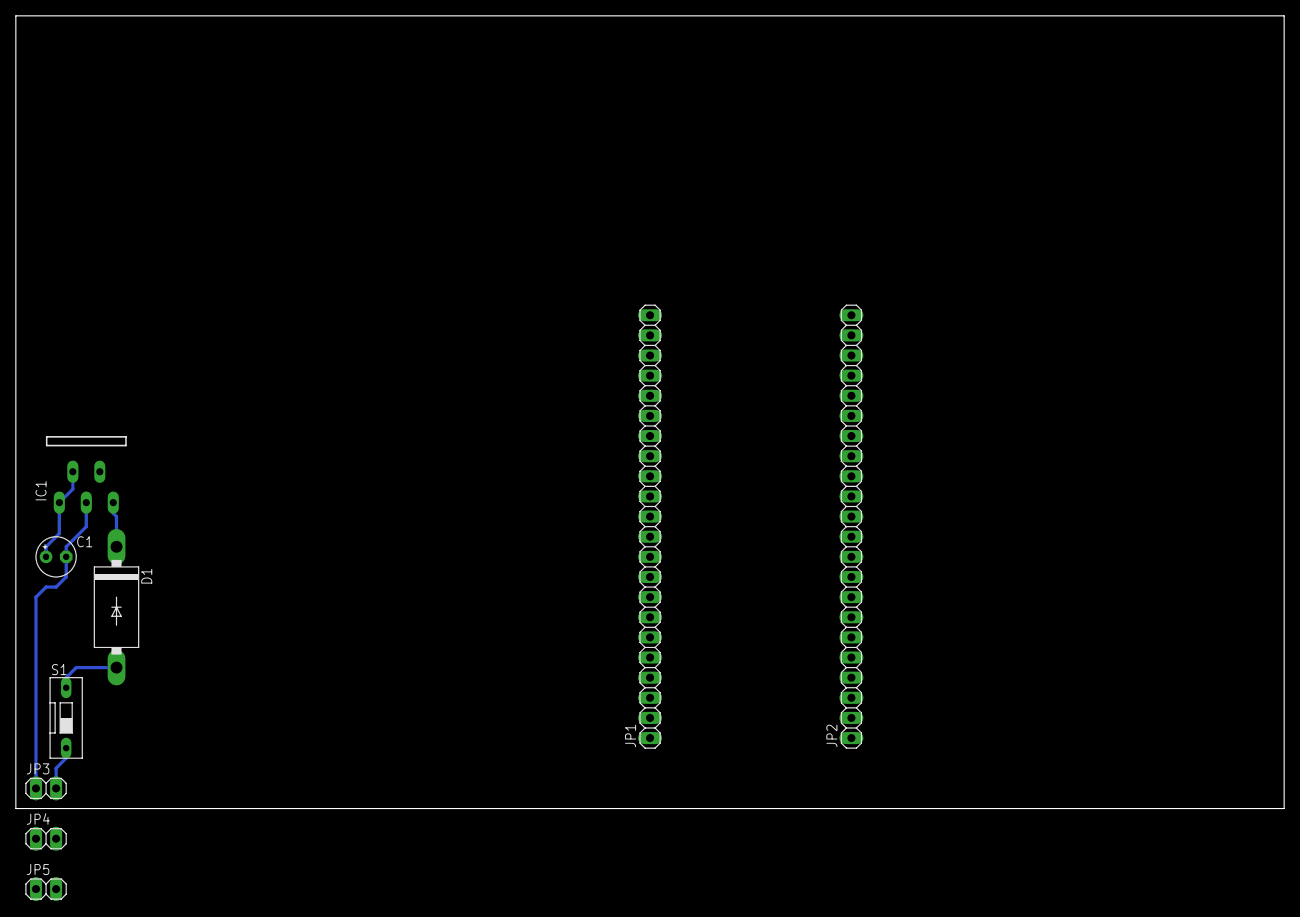
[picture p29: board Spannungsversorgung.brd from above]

Board: 2 copper layers, 160.0 x 100.0 mm, 9 parts (0 on the bottom side), 4 nets.

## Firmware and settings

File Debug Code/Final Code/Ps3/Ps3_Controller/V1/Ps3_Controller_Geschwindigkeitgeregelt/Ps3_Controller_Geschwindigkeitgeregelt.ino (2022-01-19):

#include <Servo.h>
#include <Ps3Controller.h>

int lX = 0;
int lY = 0;
int rX = 0;
int rY = 0;
#define LEDROT 14
int gesch = 0;
int posR = 0;
int L1 = 0;
int L2 = 0;
int R1 = 0;
int R2 = 0;

int ServoMerker = 0;
int ServoMerker1 = 0;
static const int servosPins[2] = {12, 13};
Servo servos[2];

void onConnect()
{
 Serial.println("IsConnected");
}

void notify(){
  Serial.println("Mainloop repeat");
 //***************************L2 & R2***************************************************?

    if( abs(Ps3.event.analog_changed.button.l1)){
       Serial.print("Pressing the left shoulder button: ");
    }

   if( 100 < abs(Ps3.event.analog_changed.button.r1) ){
       Serial.print("Pressing the right shoulder button: ");
   }

   if( abs(Ps3.event.analog_changed.button.l2) ){
       Serial.print("Pressing the left trigger button: ");
       Serial.println(Ps3.data.analog.button.l2, DEC);
   }

   if( abs(Ps3.event.analog_changed.button.r2) ){
       Serial.print("Pressing the right trigger button: ");
       Serial.println(Ps3.data.analog.button.r2, DEC);
       
            digitalWrite(LEDROT,HIGH);
   }
           else
        {
          digitalWrite(LEDROT,LOW);
        }  
  
//****************************right stick************************************************
/*
   rX =(Ps3.data.analog.stick.rx);
   rY = (Ps3.data.analog.stick.ry);
   
if(rX == -128){                       //robo nach links
  Serial.println("nach links");
      }
if(rX == 127){
    Serial.println("nach rechts");    
      } 
 if(rY == -128){                       //robo nach links
  Serial.println("nach vorne");
      }
if(rY == 127){
    Serial.println("nach hinten");    
      } 
      */
 //****************************left stick***********************************************?

Serial.println(Ps3.data.analog.stick.lx);
Serial.println(Ps3.data.analog.stick.ly);

if(Ps3.data.analog.stick.lx == -128){                       //robo nach links
  Serial.println("nach links" + lX);
  gesch = 0,7*Ps3.data.analog.stick.lx + 90;
    servos[0].write(gesch);
    servos[1].write(gesch);
      }
        else if(Ps3.data.analog.stick.lx == 127){         //robo nach rechts
         Serial.println("nach rechts" + lX);
         gesch = 0,7 * Ps3.data.analog.stick.lx + 90;
          servos[0].write(gesch);
          servos[1].write(gesch); 
            } 
        else if(Ps3.data.analog.stick.ly == -128){         //robo nach vorne                  
        Serial.println("nach vorne" + lY); 
        gesch = 0,7 * Ps3.data.analog.stick.ly + 90;
    servos[0].write(gesch);
    servos[1].write(gesch);
            } 
        else if(Ps3.data.analog.stick.ly >= 127){           //robo nach hinten
          Serial.println("nach hinten" + lY); 
          gesch = 0,7 * Ps3.data.analog.stick.ly + 90;
          
          servos[0].write(gesch);
          servos[1].write(gesch);  
            }
        else
            {
            servos[0].write(90);
            servos[1].write(90);  
            }
          
     
//****************************cross right side*******************************************
if( Ps3.data.button.cross ){
            Serial.println("Pressing the cross button");      //Pressing the cross button(X)
        }


if( Ps3.data.button.square ){
            Serial.println("Pressing the square button");     //Pressing the square button([])
        }

if( Ps3.data.button.triangle ){
            Serial.println("Pressing the triangle button");   //Pressing the triangle button
        }

if( Ps3.data.button.circle ){
            Serial.println("Pressing the circle button");     //Pressing the circle button
        }
  //****************************cross right side*******************************************?

  
}

void setup() {
  //******************************servo***************************
pinMode(LEDROT, OUTPUT);
for(int i = 0; i < 2; ++i) {
        if(!servos[i].attach(servosPins[i])) {
        Serial.print("Servo ");
        Serial.print(i);
        Serial.println("attach error");
        }
    }
    Serial.begin(115200);
    Ps3.begin("00:13:a9:e0:cd:a9");
    Ps3.attachOnConnect(onConnect);
    
    
    Ps3.attach(notify);
      
    
    
    Serial.println("Ready.");


}

void loop() 
{
  
if(Ps3.isConnected()){
            return;
            delay(1000);
         }

}

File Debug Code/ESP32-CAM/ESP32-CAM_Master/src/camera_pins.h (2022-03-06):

#if defined(CAMERA_MODEL_WROVER_KIT)
#define PWDN_GPIO_NUM    -1
#define RESET_GPIO_NUM   -1
#define XCLK_GPIO_NUM    21
#define SIOD_GPIO_NUM    26
#define SIOC_GPIO_NUM    27

#define Y9_GPIO_NUM      35
#define Y8_GPIO_NUM      34
#define Y7_GPIO_NUM      39
#define Y6_GPIO_NUM      36
#define Y5_GPIO_NUM      19
#define Y4_GPIO_NUM      18
#define Y3_GPIO_NUM       5
#define Y2_GPIO_NUM       4
#define VSYNC_GPIO_NUM   25
#define HREF_GPIO_NUM    23
#define PCLK_GPIO_NUM    22

#elif defined(CAMERA_MODEL_ESP_EYE)
#define PWDN_GPIO_NUM    -1
#define RESET_GPIO_NUM   -1
#define XCLK_GPIO_NUM    4
#define SIOD_GPIO_NUM    18
#define SIOC_GPIO_NUM    23

#define Y9_GPIO_NUM      36
#define Y8_GPIO_NUM      37
#define Y7_GPIO_NUM      38
#define Y6_GPIO_NUM      39
#define Y5_GPIO_NUM      35
#define Y4_GPIO_NUM      14
#define Y3_GPIO_NUM      13
#define Y2_GPIO_NUM      34
#define VSYNC_GPIO_NUM   5
#define HREF_GPIO_NUM    27
#define PCLK_GPIO_NUM    25

#elif defined(CAMERA_MODEL_M5STACK_PSRAM)
#define PWDN_GPIO_NUM     -1
#define RESET_GPIO_NUM    15
#define XCLK_GPIO_NUM     27
#define SIOD_GPIO_NUM     25
#define SIOC_GPIO_NUM     23

#define Y9_GPIO_NUM       19
#define Y8_GPIO_NUM       36
#define Y7_GPIO_NUM       18
#define Y6_GPIO_NUM       39
#define Y5_GPIO_NUM        5
#define Y4_GPIO_NUM       34
#define Y3_GPIO_NUM       35
#define Y2_GPIO_NUM       32
#define VSYNC_GPIO_NUM    22
#define HREF_GPIO_NUM     26
#define PCLK_GPIO_NUM     21

#elif defined(CAMERA_MODEL_M5STACK_V2_PSRAM)
#define PWDN_GPIO_NUM     -1
#define RESET_GPIO_NUM    15
#define XCLK_GPIO_NUM     27
#define SIOD_GPIO_NUM     22
#define SIOC_GPIO_NUM     23

#define Y9_GPIO_NUM       19
#define Y8_GPIO_NUM       36
#define Y7_GPIO_NUM       18
#define Y6_GPIO_NUM       39
#define Y5_GPIO_NUM        5
#define Y4_GPIO_NUM       34
#define Y3_GPIO_NUM       35
#define Y2_GPIO_NUM       32
#define VSYNC_GPIO_NUM    25
#define HREF_GPIO_NUM     26
#define PCLK_GPIO_NUM     21

#elif defined(CAMERA_MODEL_M5STACK_WIDE)
#define PWDN_GPIO_NUM     -1
#define RESET_GPIO_NUM    15
#define XCLK_GPIO_NUM     27
#define SIOD_GPIO_NUM     22
#define SIOC_GPIO_NUM     23

#define Y9_GPIO_NUM       19
#define Y8_GPIO_NUM       36
#define Y7_GPIO_NUM       18
#define Y6_GPIO_NUM       39
#define Y5_GPIO_NUM        5
#define Y4_GPIO_NUM       34
#define Y3_GPIO_NUM       35
#define Y2_GPIO_NUM       32
#define VSYNC_GPIO_NUM    25
#define HREF_GPIO_NUM     26
#define PCLK_GPIO_NUM     21

#elif defined(CAMERA_MODEL_M5STACK_ESP32CAM)
#define PWDN_GPIO_NUM     -1
#define RESET_GPIO_NUM    15
#define XCLK_GPIO_NUM     27
#define SIOD_GPIO_NUM     25
#define SIOC_GPIO_NUM     23

#define Y9_GPIO_NUM       19
#define Y8_GPIO_NUM       36
#define Y7_GPIO_NUM       18
#define Y6_GPIO_NUM       39
#define Y5_GPIO_NUM        5
#define Y4_GPIO_NUM       34
#define Y3_GPIO_NUM       35
#define Y2_GPIO_NUM       17
#define VSYNC_GPIO_NUM    22
#define HREF_GPIO_NUM     26
#define PCLK_GPIO_NUM     21

#elif defined(CAMERA_MODEL_AI_THINKER)
#define PWDN_GPIO_NUM     32
#define RESET_GPIO_NUM    -1
#define XCLK_GPIO_NUM      0
#define SIOD_GPIO_NUM     26
#define SIOC_GPIO_NUM     27

#define Y9_GPIO_NUM       35
#define Y8_GPIO_NUM       34
#define Y7_GPIO_NUM       39
#define Y6_GPIO_NUM       36
#define Y5_GPIO_NUM       21
#define Y4_GPIO_NUM       19
#define Y3_GPIO_NUM       18
#define Y2_GPIO_NUM        5
#define VSYNC_GPIO_NUM    25
#define HREF_GPIO_NUM     23
#define PCLK_GPIO_NUM     22

#elif defined(CAMERA_MODEL_TTGO_T_JOURNAL)
#define PWDN_GPIO_NUM      0
#define RESET_GPIO_NUM    15
#define XCLK_GPIO_NUM     27
#define SIOD_GPIO_NUM     25
#define SIOC_GPIO_NUM     23

#define Y9_GPIO_NUM       19
#define Y8_GPIO_NUM       36
#define Y7_GPIO_NUM       18
#define Y6_GPIO_NUM       39
#define Y5_GPIO_NUM        5
#define Y4_GPIO_NUM       34
#define Y3_GPIO_NUM       35
#define Y2_GPIO_NUM       17
#define VSYNC_GPIO_NUM    22
#define HREF_GPIO_NUM     26
#define PCLK_GPIO_NUM     21

#else
#error "Camera model not selected"
#endif

#ifndef ESP32_CAM_MASTER_CAMERA_PINS_H
#define ESP32_CAM_MASTER_CAMERA_PINS_H

#endif //ESP32_CAM_MASTER_CAMERA_PINS_H

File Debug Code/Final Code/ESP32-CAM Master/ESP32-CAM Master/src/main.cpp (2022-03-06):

#include <Arduino.h>
#include "esp_camera.h"
#include <WiFi.h>
#include <Ps3Controller.h>
#include <ESP32Servo.h>

#include "soc/soc.h"
#include "soc/rtc_cntl_reg.h"

#define MYPORT_TX 13
#define MYPORT_RX 14

#define stopSendTimeout 1
#define resetSendTimeout 5000

#define CAMERA_MODEL_AI_THINKER // Has PSRAM

#include "camera_pins.h"

const char *ssid = "Danladman";
const char *password = "lol123456";
IPAddress staticIP(192, 168, 1, 110);     // Master ESP32-CAM: 110
IPAddress gateway(192, 168, 1, 1);
IPAddress subnet(255, 255, 255, 0);

static const int servosPins[2] = {12, 2};
Servo servos[2];

void startCameraServer();

void onConnect();

void checkPS3Controller();

bool lockIRSender = false;                  // Lock for bluetooth-controlled shooting action
unsigned long infraRedSendTimestamp = 0;    // Timestamp for IR-lock

void setup() {
    delay(500);
    WRITE_PERI_REG(RTC_CNTL_BROWN_OUT_REG, 0);          // Disable brownout detector !! WARNING !!
    Serial.begin(115200);
    Serial.setDebugOutput(true);
    Serial.println();

    Serial2.begin(9600, SERIAL_8N1, MYPORT_RX, MYPORT_TX);

    Ps3.attachOnConnect(onConnect);
    Ps3.begin("00:13:a9:e0:cd:a9");

    camera_config_t config;
    config.ledc_channel = LEDC_CHANNEL_3;
    config.ledc_timer = LEDC_TIMER_1;
    config.pin_d0 = Y2_GPIO_NUM;
    config.pin_d1 = Y3_GPIO_NUM;
    config.pin_d2 = Y4_GPIO_NUM;
    config.pin_d3 = Y5_GPIO_NUM;
    config.pin_d4 = Y6_GPIO_NUM;
    config.pin_d5 = Y7_GPIO_NUM;
    config.pin_d6 = Y8_GPIO_NUM;
    config.pin_d7 = Y9_GPIO_NUM;
    config.pin_xclk = XCLK_GPIO_NUM;
    config.pin_pclk = PCLK_GPIO_NUM;
    config.pin_vsync = VSYNC_GPIO_NUM;
    config.pin_href = HREF_GPIO_NUM;
    config.pin_sscb_sda = SIOD_GPIO_NUM;
    config.pin_sscb_scl = SIOC_GPIO_NUM;
    config.pin_pwdn = PWDN_GPIO_NUM;
    config.pin_reset = RESET_GPIO_NUM;
    config.xclk_freq_hz = 20000000;
    config.pixel_format = PIXFORMAT_JPEG;

    // if PSRAM IC present, init with UXGA resolution and higher JPEG quality
    //                      for larger pre-allocated frame buffer.
    if (psramFound()) {
        config.frame_size = FRAMESIZE_UXGA;
        config.jpeg_quality = 10;
        config.fb_count = 2;
    } else {
        config.frame_size = FRAMESIZE_SVGA;
        config.jpeg_quality = 12;
        config.fb_count = 1;
    }

    // camera init
    esp_err_t err = esp_camera_init(&config);
    if (err != ESP_OK) {
        Serial.printf("Camera init failed with error 0x%x", err);
        return;
    }

    sensor_t *s = esp_camera_sensor_get();
    // initial sensors are flipped vertically and colors are a bit saturated
    if (s->id.PID == OV3660_PID) {
        s->set_vflip(s, 1); // flip it back
        s->set_brightness(s, 1); // up the brightness just a bit
        s->set_saturation(s, -2); // lower the saturation
    }
    // drop down frame size for higher initial frame rate
    s->set_framesize(s, FRAMESIZE_QVGA);

    WiFi.config(staticIP, gateway, subnet);
    WiFi.begin(ssid, password);

    while (WiFi.status() != WL_CONNECTED) {
        delay(500);
        Serial.print(".");
    }
    Serial.println("");
    Serial.println("WiFi connected");

    startCameraServer();

    Serial.print("Camera Ready! Use 'http://");
    Serial.print(WiFi.localIP());
    Serial.println("' to connect");

    for(int i = 0; i < 2; ++i) {
        if (!servos[i].attach(servosPins[i])) {
            Serial.print("Servo ");
            Serial.print(i);
            Serial.println("attach error");
        }
    }
}

void loop() {
    checkPS3Controller();

    if (lockIRSender) {
        if ((millis() - infraRedSendTimestamp) >= resetSendTimeout) {
            lockIRSender = false;
        }
        if ((millis() - infraRedSendTimestamp) < stopSendTimeout) {
            Serial2.write('y');
        }
    }
}

void checkPS3Controller() {
    if(Ps3.data.analog.stick.lx == -128){                       //robo nach links
        // Serial.println("nach links" + lX);
        servos[0].write(0);
        servos[1].write(0);
    }
    else if(Ps3.data.analog.stick.lx == 127){         //robo nach rechts
        // Serial.println("nach rechts" + lX);

        servos[0].write(180);
        servos[1].write(180);
    }
    else if(Ps3.data.analog.stick.ly == -128){         //robo nach vorne
        // Serial.println("nach vorne" + lY);
        servos[0].write(0);
        servos[1].write(180);
    }
    else if(Ps3.data.analog.stick.ly >= 127){           //robo nach hinten
        // Serial.println("nach hinten" + lY);

        servos[0].write(180);
        servos[1].write(0);
    }
    else
    {
        servos[0].write(90);
        servos[1].write(90);
    }
//    if (Ps3.event.analog_changed.button.r2 || Ps3.event.analog_changed.button.l2) {
//        Serial2.write('y');
//    }

    if (!lockIRSender) {  // TODO: Lock IRremote and send to LED
        if (Ps3.event.analog_changed.button.r2 || Ps3.event.analog_changed.button.l2) {
            lockIRSender = true;
            infraRedSendTimestamp = millis();
        }
    }
}

void onConnect() {
    Serial.println("Successfully connected PS3 controller.");
}

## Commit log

2021-10-06 Included the Eagel Schematic and Board
    [Spannungsversorgung.brd, Spannungsversorgung.sch]
2021-10-15 Added 'IR-robo-motor' test program
2021-11-10 Added PinHeads to the Eagle file
    [Spannungsversorgung.sch]
2021-12-01 Added Features & Verwendung to the documentation of LT1529-5
    [Spannungsversorgung.brd, Spannungsversorgung.sch]
2021-12-22 beginn of the Servo
2022-01-14 change of code for servo
2022-01-15 Servos are Working now. Added new File for a new Version of The ps3_Code
2022-01-26 Documentary of Ps3_Controller & Servo
2022-02-10 Improved data exchange over WiFi between the two ESP32-CAMs
2022-02-17 The problem that came with switching from esp32 to esp32S2
    [Ps3_Controller.ino, main.cpp]
2022-03-07 Added pin description for PCB-design
2022-03-20 Added the final version for the PCB to the repo
    [Spannungsversorgung_FinalVersion.brd, Spannungsversorgung_FinalVersion.sch, Spannungsversorgung_V1.brd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]
2022-03-30 Add a schematic for the communication between the devices
